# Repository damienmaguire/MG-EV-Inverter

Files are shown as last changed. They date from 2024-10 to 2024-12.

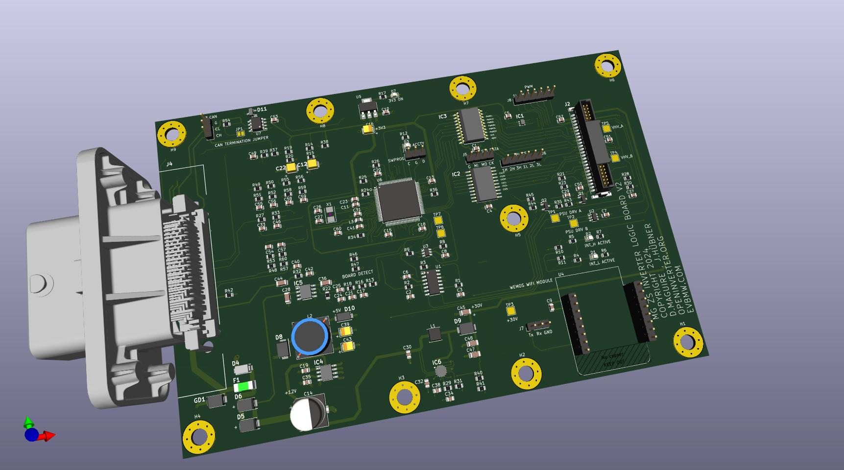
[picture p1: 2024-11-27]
Design/Breakout/V2/MG_ZS_V2_3D.jpg

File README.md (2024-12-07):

# MG-EV-Inverter
Reverse engineering of the drive motor and inverter used in MG Electric Vehicles.

The drive unit here is from a 2022 MG ZS EV Right hand drive. 

First look : https://vimeo.com/929258328

IGBT Module : FS820R08A6P2B

Gate driver : MC33GD3100EK

One current sensor per phase. 5V supply, 2.5V at zero current anlog output.

Isolated gate power supplies provided from a common 30VDC primary supply , a pair of 5V at 132KHz and 42% duty signals to a mosfet driver. Transformers are Epcos A213721495C.

HV Voltage sensing is achived using the external ADC channel of the Low3 gate driver and transmitted via spi.

The three IGBT temp sensors are fed into the relevant high side drivers. Temp is sensed using the external ADC channel of the  three high side gate drivers and transmitted via spi.

The OEM logic board communicates with all 6 gate drive chips via SPI at a clock rate of 1.7MHz. Data is in 16 bit format with an 8 bit crc and sent/received as 24 bit packets.
Sadly , NXP want an NDA to allow access to the SPI data for this device. As this would then tie me down from sharing the data I will not be going this route. Instead, we'll use reverse engineering and open
information to discern the data formatting.

Freely available information has been found here :

https://community.nxp.com/t5/Other-NXP-Products/MC33GD3100-daisy-chain/td-p/1309335

and

https://community.nxp.com/t5/Power-Management/CRC-seed-value-for-MC33GD3100/m-p/1677961

and

https://community.nxp.com/t5/Motor-Control-and-Smart-Energy/GD3160-SPI-Example-code-Question/m-p/1780583

A series of SPI logic analyser captures are now here on the repo. Files are in Saleae Logic 2 format which my be freely downloaded here : https://www.saleae.com/pages/downloads

An Openinverter logic board replacement is currently being designed to allow this drive unit to be used unrestricted. Design files will be in Kicad format : https://www.kicad.org/

The external power and signal connector is a Molex 500762-1001 available from Mouser : https://www.mouser.ie/ProductDetail/538-500762-1001

A pre wired 48 way plug to fit this is available from AliExpress : 
https://www.aliexpress.com/item/1005004818455812.html

The logic board to power board connector is a ERNI 063210-E available from Mouser : https://www.mouser.ie/ProductDetail/305-063210

The motor resolver and temp sensor connector is a TE 1897462-2 available from Mouser : https://www.mouser.ie/ProductDetail/571-1897462-2
Pins : https://www.mouser.ie/ProductDetail/571-7-1452656-3-CT

Gate driver signals are 5V level. One active low fault / INT line for high and low sides.

HV Connector may be Yonguui Metal Housing Connector-YG998C

V2 Logic board now undergoing testing.

Now working in closed loop FOC control with V2 logic board : https://vimeo.com/1032344714

Added 3D printable HV connector replacement. Also available on Printables : https://www.printables.com/model/1100211-mg-ev-drive-unit-high-voltage-connector

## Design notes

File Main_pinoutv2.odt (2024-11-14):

MG DU Logic Board Main Connector

Function Pin

CANH A3

CANL A4

FORWARD DIRECTION B3

REVERSE DIRECTION B4

BRAKE INPUT C3

MOTOR TEMP SENSE 1 F3

MOTOR TEMP SENSE 2 F4

SINB G3

SINA G4

COSB H3

COSA H4

ACCEL +5V J1

ACCEL SIGNAL A J2

ACCEL SIGNAL B J3

ACCEL GND J4

START SIGNAL K4

EXCA L3

EXCB L4

+12V SUPPLY M3

MAIN GROUND M4

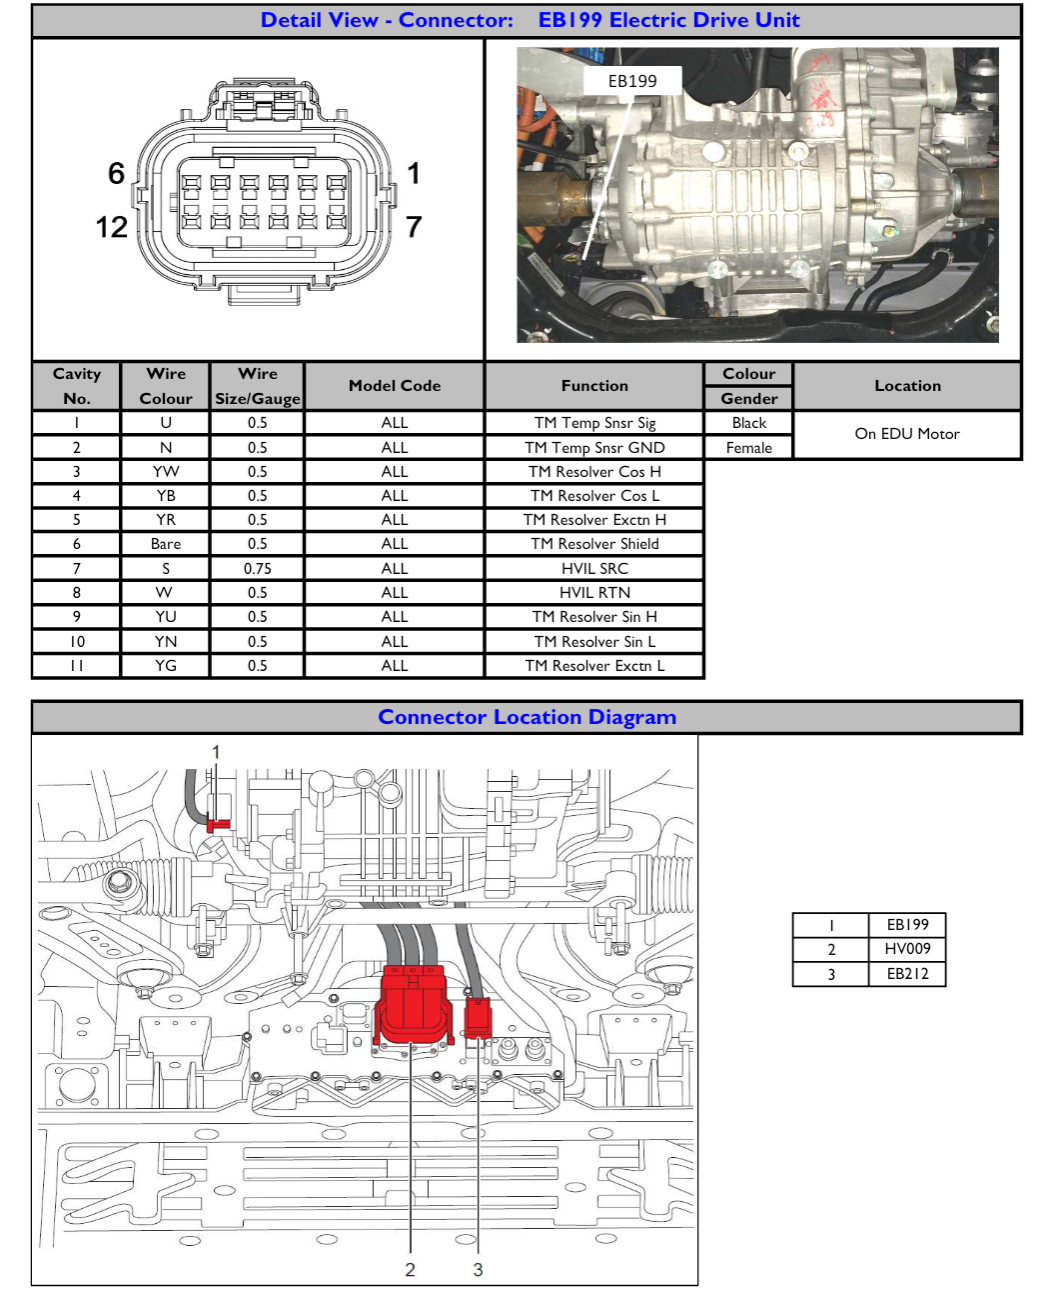
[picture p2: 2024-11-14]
Resolver_plug.png

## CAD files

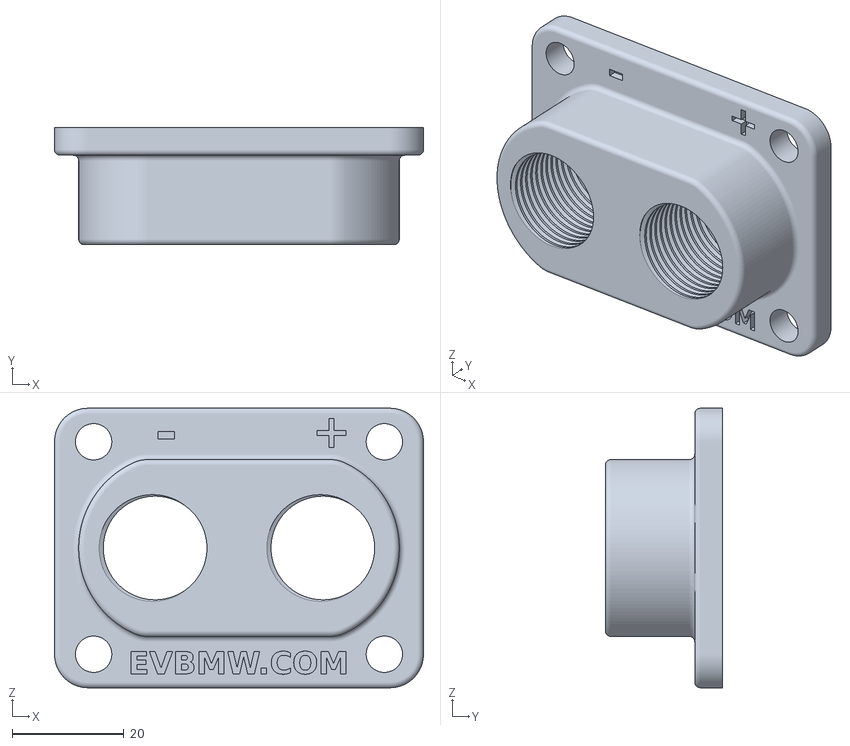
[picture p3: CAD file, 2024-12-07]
3D_Printable_Parts/HV_Gland_Plate.stl
66.0 x 21.0 x 50.0

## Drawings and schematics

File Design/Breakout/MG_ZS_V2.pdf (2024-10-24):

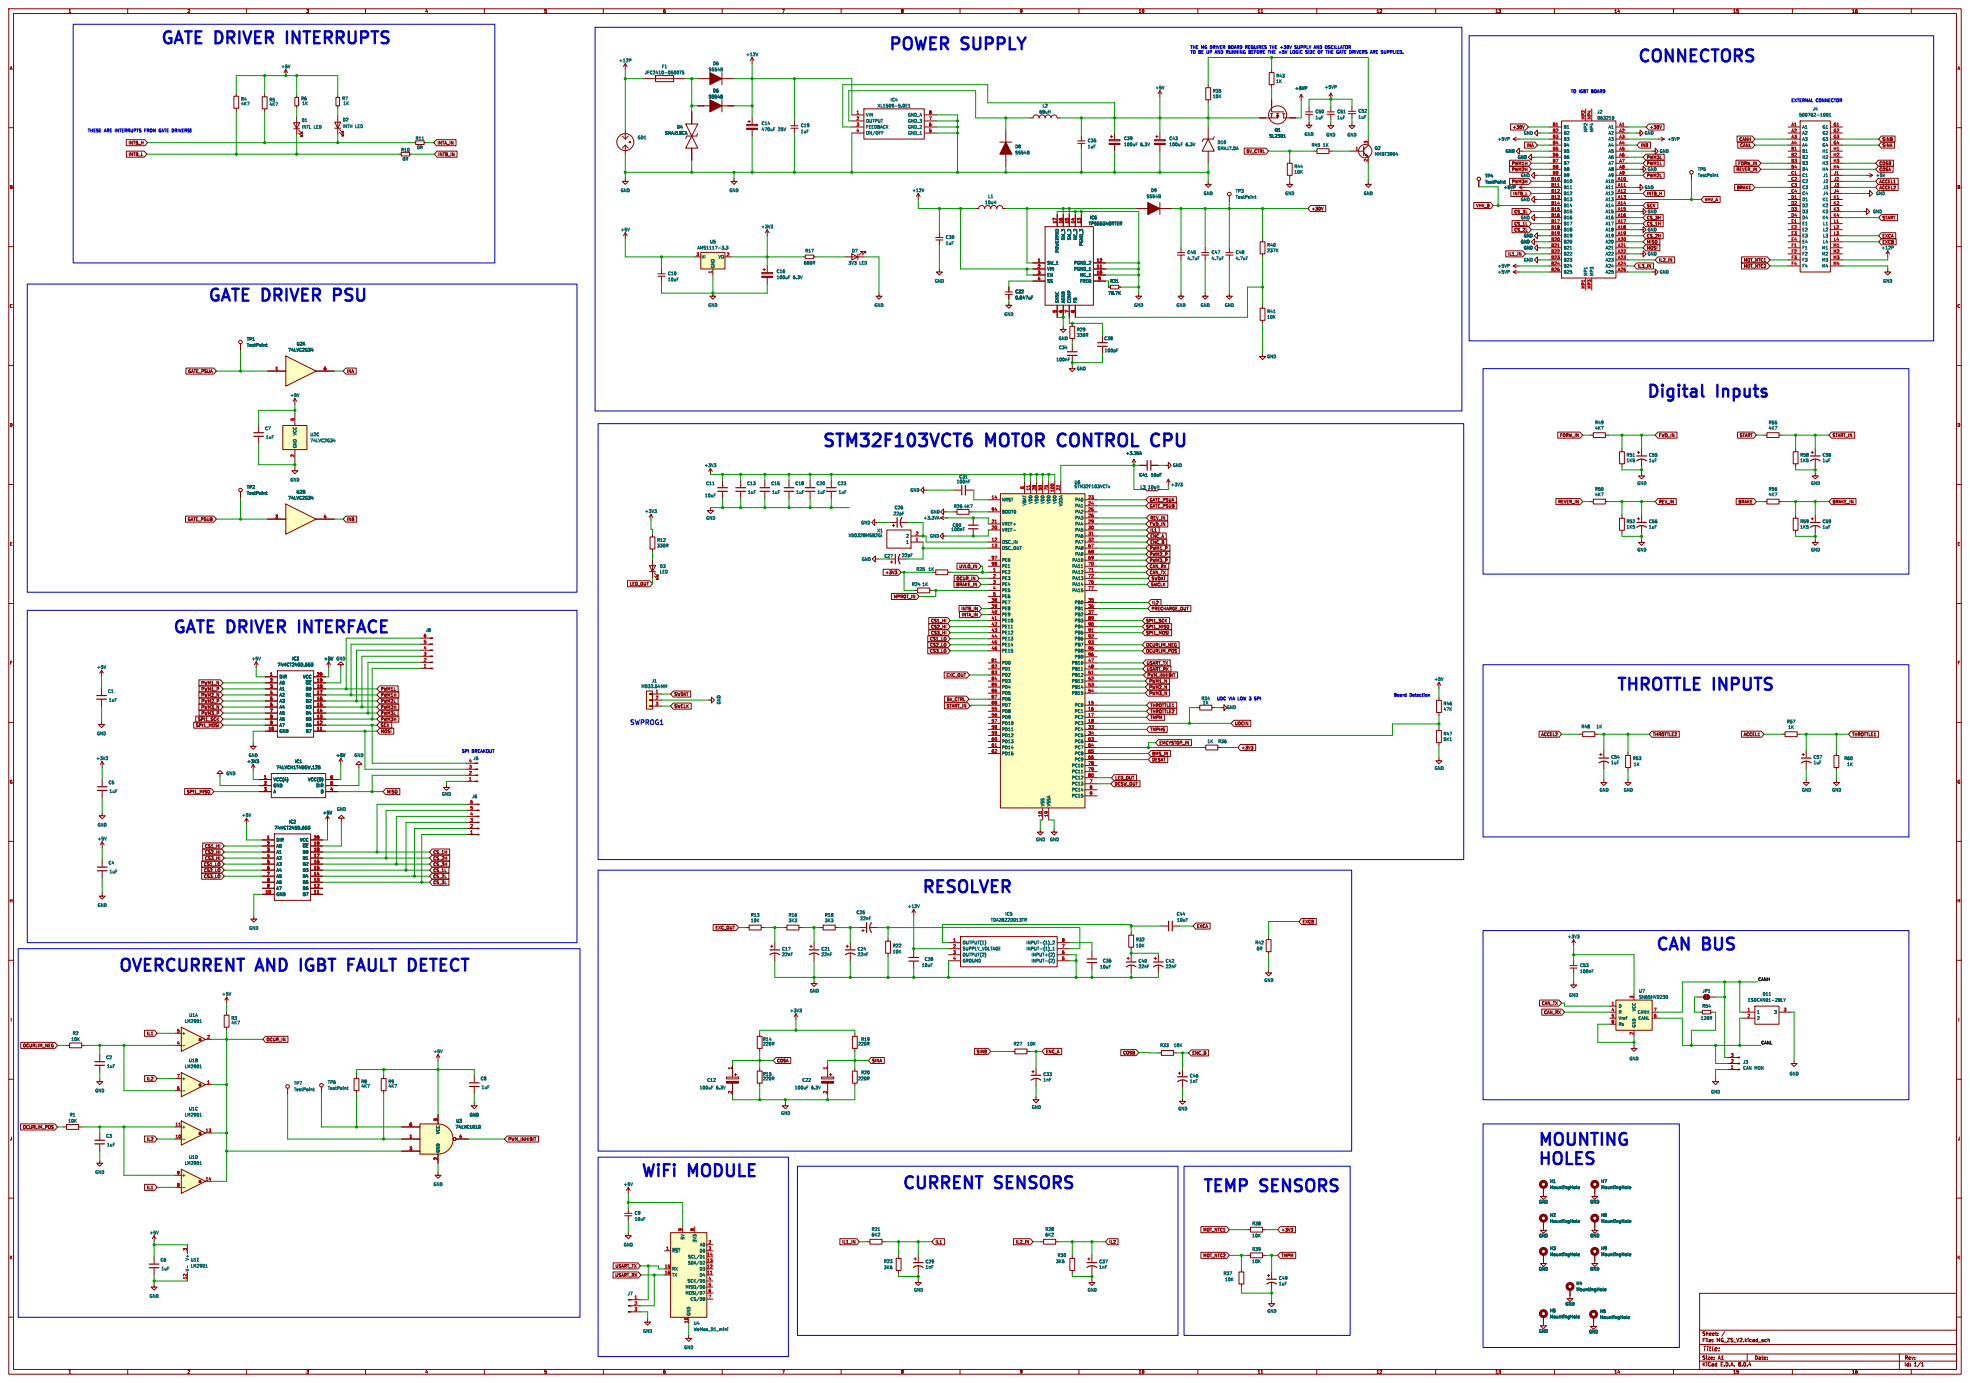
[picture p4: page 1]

THE MG DRIVER BOARD REQUIRES THE +30V SUPPLY AND OSCILLATOR

TO BE UP AND RUNNING BEFORE THE +5V LOGIC SIDE OF THE GATE DRIVERS ARE SUPPLIED. RESOLVER

THESE ARE INTERRUPTS FROM GATE DRIVERS! OVERCURRENT AND IGBT FAULT DETECT

UDC VIA LOW 3 SPI GATE DRIVER PSU
74LVC2G34 TP1 TestPoint

Id: 1/1 Title: File: MG_ZS_V2.kicad_sch Sheet: /

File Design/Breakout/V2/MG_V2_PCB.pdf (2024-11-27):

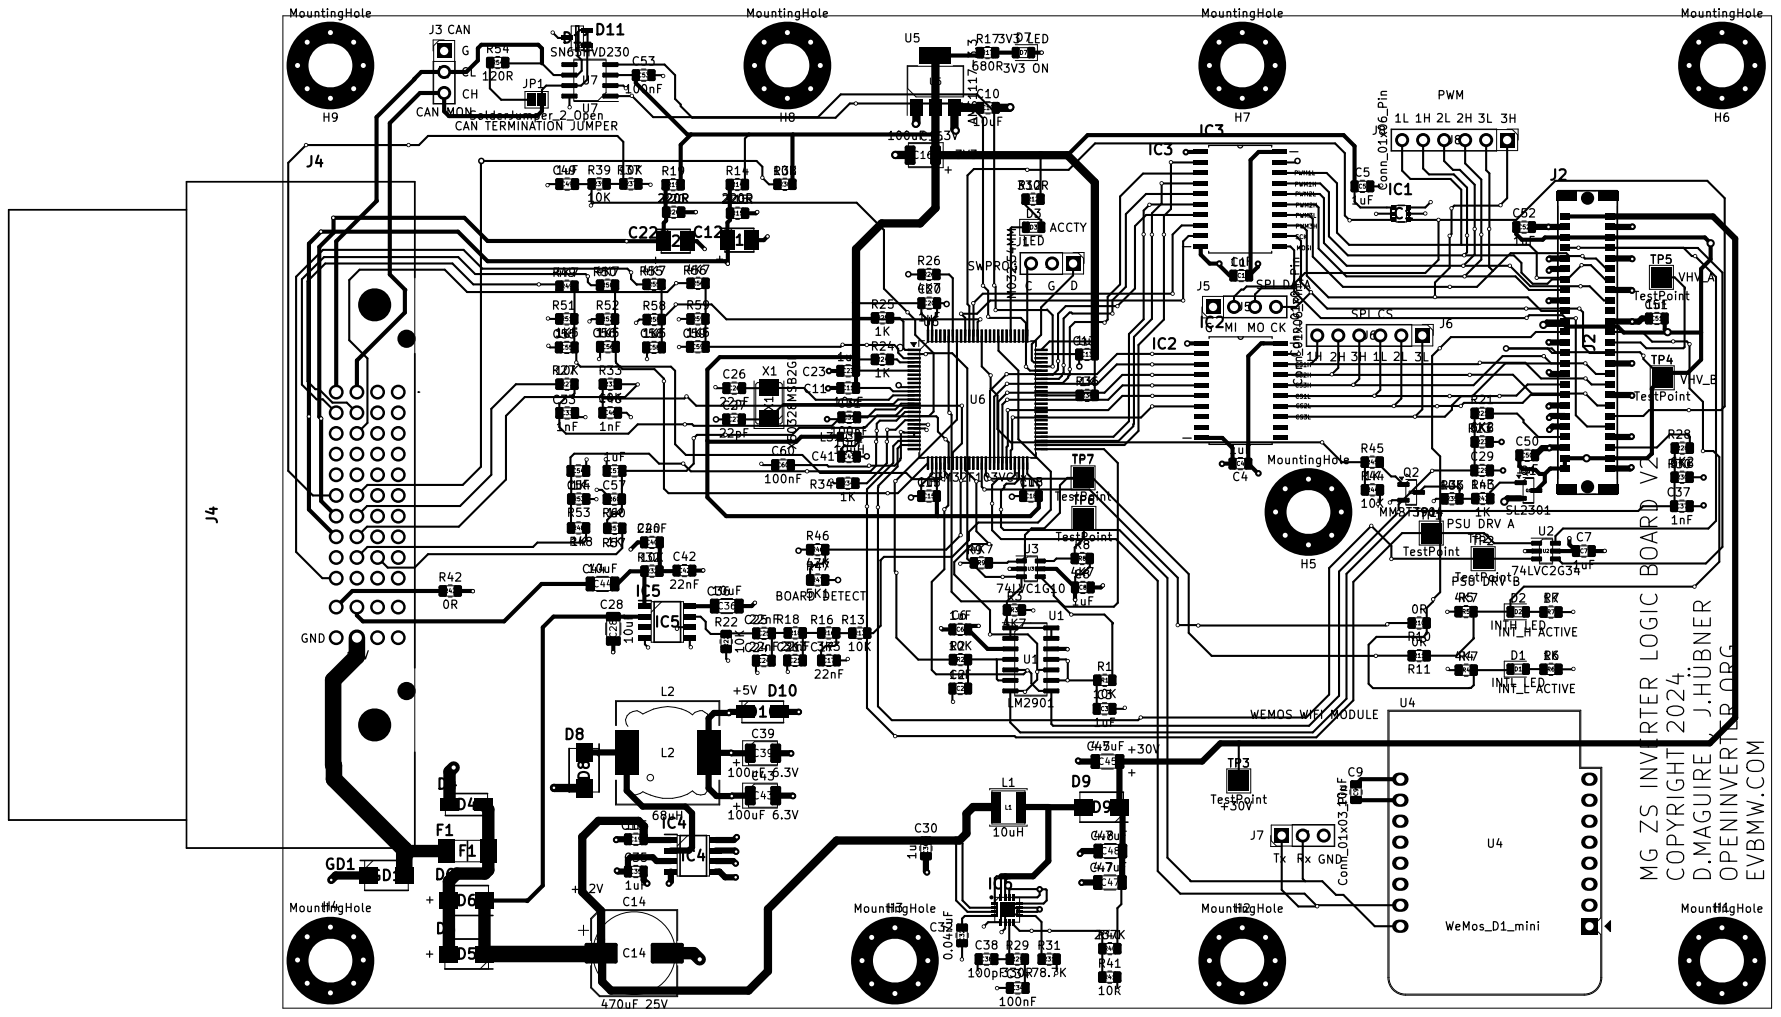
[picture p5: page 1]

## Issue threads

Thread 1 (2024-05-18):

Can_OBD2.cpp

peterdiffey, 2024-05-18:
#include "Can_OBD2.h"
#include "stm32_can.h"
#include "params.h" <<<<<< not in repo

params.h does not exist, however there is a params_prj.h

I have been having trouble with getting RPM out of canbus.
I am not a C++ programmer, so I be talking tosh, but that params.h  file missing may have impact.

I note the following  in Can_OBD2.cpp
====================================
void Can_OBD2::DecodeCAN(int id, uint32_t data[2])
{
  uint8_t *bytes = (uint8_t *)data; // arrgghhh this converts the two 32bit array into bytes. See comments are useful:)
  uint8_t response[8];
  uint16_t speed;

  if (id == 0x7DF)   or better if (id == PID_REQUEST)

where does this id come from? ie who/what is sending a can msg (presumably) starting 0x7DF

====================================
      case ENGINE_RPM:
        response[0] = 0x04;
        response[2] = ENGINE_RPM;
        speed = Param::GetInt(Param::speed);   <<< is this a parameter or is this data?
        response[3] = (speed >> 8) & 0xFF;
        response[4] = (speed) & 0xFF;
        can->Send(PID_REPLY, response, 8);
        break;

Param::GetInt(Param::speed); is surely getting the value set in the webUI called speed, so it will always report whatever is set in the webUI

damienmaguire, 2024-12-14:
This has no bearing on the MG inverter project.

Closed 2024-12-14.

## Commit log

2024-04-05 Add breakout board gerber
2024-10-24 Add V2 Logic Board Schematic
2024-11-27 Add V2 Schematic and board layout
2024-11-27 Add V2 3D board view
2024-12-07 Add V2 Logic Board Gerber Files
2024-12-07 Add stl file for M20 gland plate
    [HV_Gland_Plate.stl]
